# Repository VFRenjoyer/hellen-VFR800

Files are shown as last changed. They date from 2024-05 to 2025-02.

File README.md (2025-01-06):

This repo contains files to build a standalone plug and play RusEFI Hellen based ECU for a 99 Honda VFR800. The prototype is unfinished and currently none of these files can be used to make a functioning ECU

This hardware may be compatible with the CBR600F4i, CBR929RR, and 01-03 CBR1100xx  if the ECU connectors were repinned.

In addition to the above it may be able to replace the ignition module/ECU of a 98-08 VT1100C, 01-07 VT750DC, 02-04 VTX1800, RC51, and 2003-09 VTX1300 with some harness repinning

Features in progress as of v0.05A:

Drop in ECU replacement for 99-01 VFR800 with addition of 2 wideband oxygen sensors

4x sequential ignition/injection

CANBUS

2x Wideband oxygen sensor channels

3x lowside driver output on rear connector

Inputs for analog sensor on rear connector

USB support

Bluetooth connectivity

MicroSD card for logging

VSS input to ECU for eventual implementation of traction control

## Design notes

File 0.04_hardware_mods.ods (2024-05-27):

Modification | Reason
470k resistor between 12V and Tach pin | Tach needs >10v pulses to work
Remove both 22uf capacitors from next to SD card slot | 3.3v current limiting on startup, mentioned on uaEFI github
Replace SMD pull up resistors on MCU analog pins with correct values from uaEFI rev A BOM | Almost all of these are wrong, refer to BOM
Add voltage divider to CRANK/CAM- pin to create +500mV offset | VR Discrete Cam signal drops out at higher frequencies when there’s a signal on the Crank input unless there’s an offset on Cam/Crank negative pin

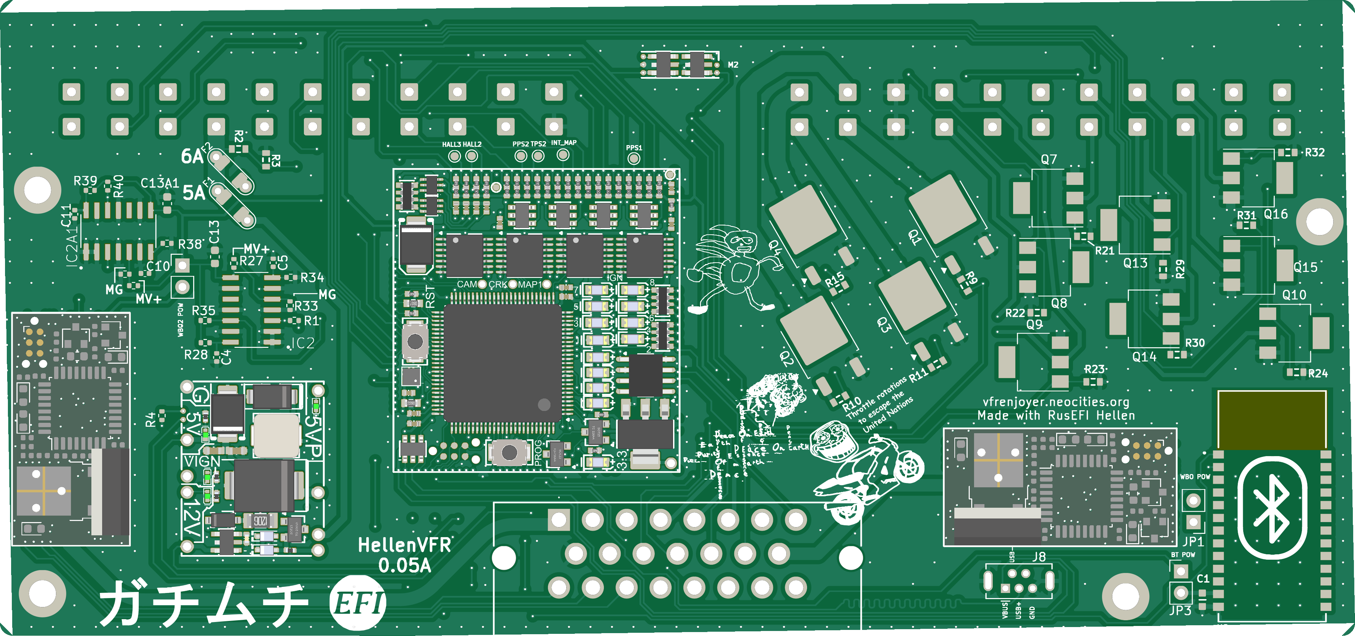
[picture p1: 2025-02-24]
boards/VFRECU-VR-0.05/board/VFRECU-VR-0.05.png

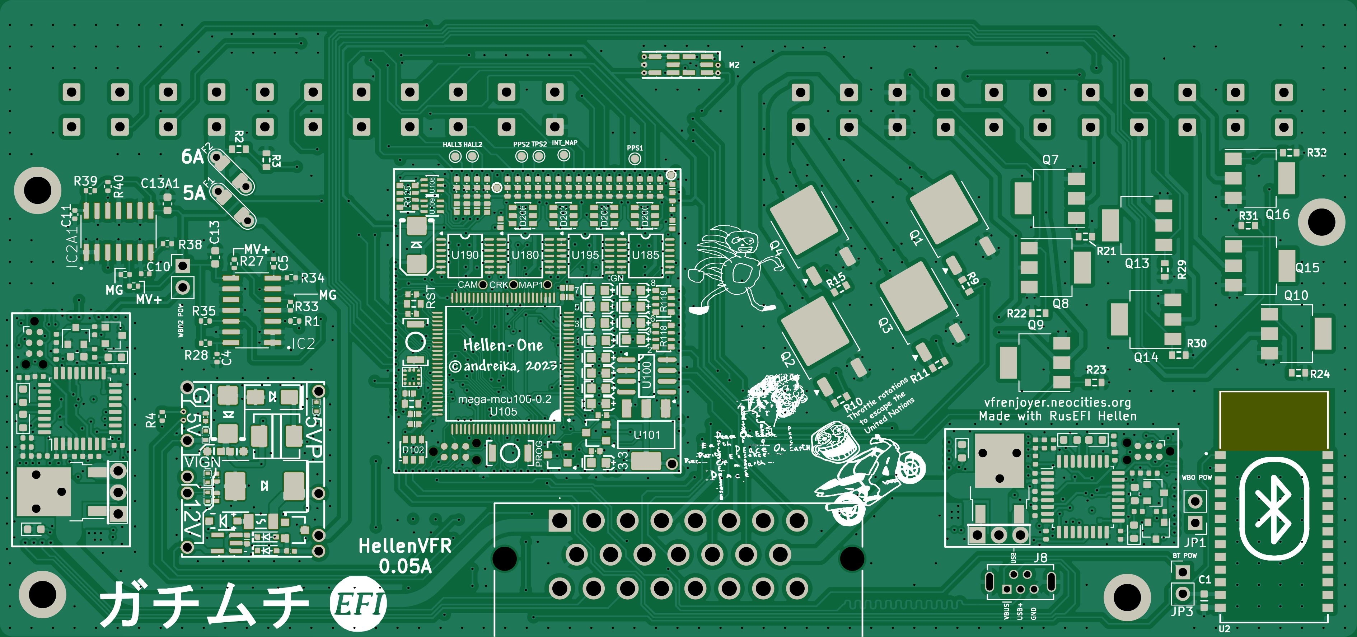
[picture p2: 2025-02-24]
boards/VFRECU-VR-0.05/board/misc/VFRECU-VR-0.05-top.png

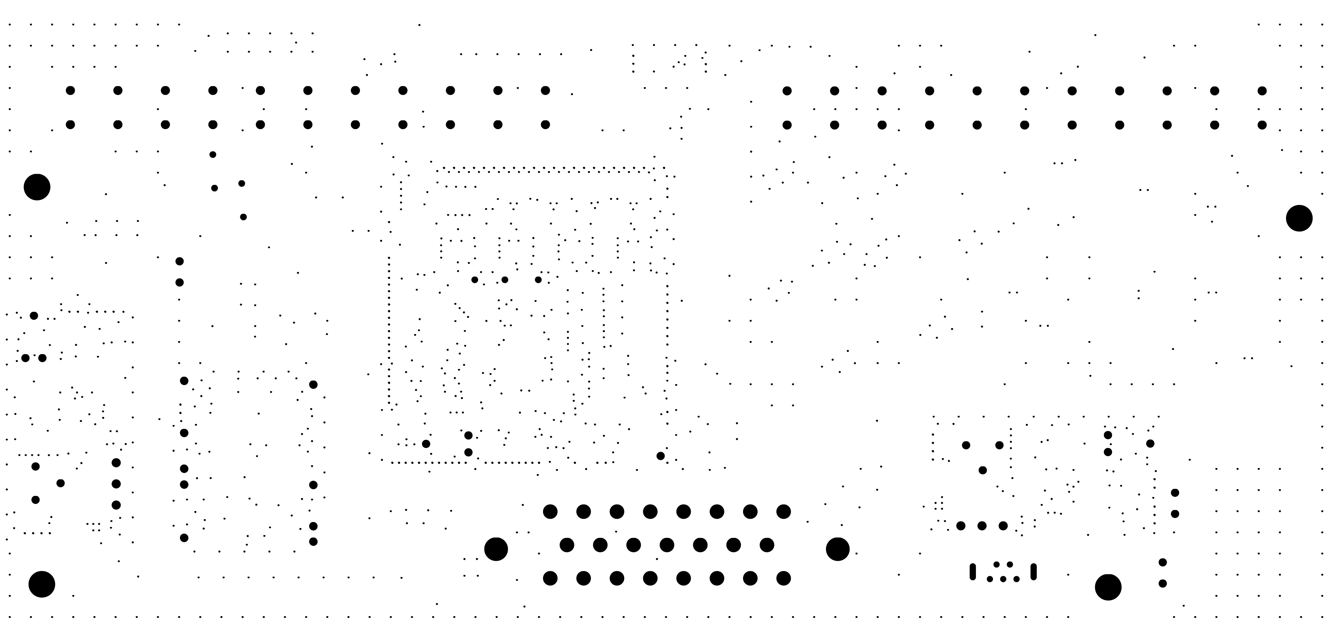
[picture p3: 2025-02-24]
boards/VFRECU-VR-0.05/board/misc/VFRECU-VR-0.05-outline.png

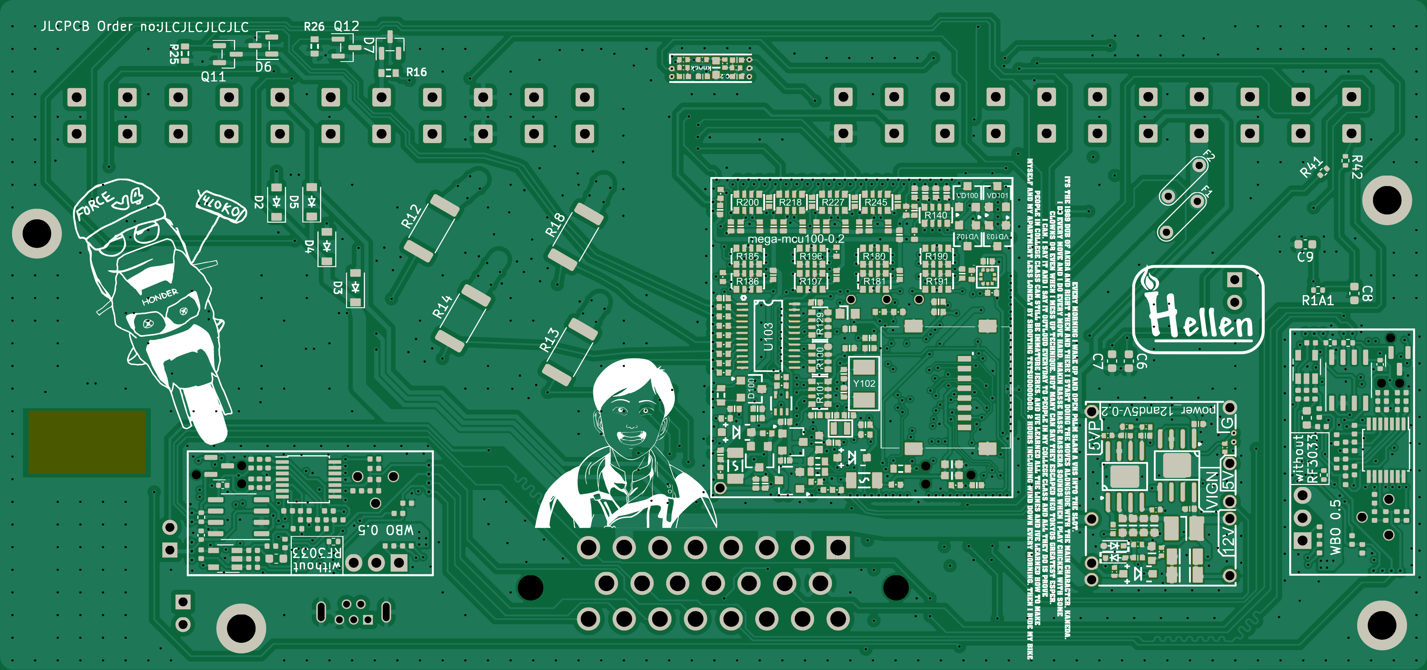
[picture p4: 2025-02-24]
boards/VFRECU-VR-0.05/board/misc/VFRECU-VR-0.05-bottom.png

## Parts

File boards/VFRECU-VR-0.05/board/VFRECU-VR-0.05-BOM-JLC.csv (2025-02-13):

Comment | Designator | Footprint | LCSC Part #
100n | C1 | C0603 | C14663
10u | C13, C13A1, C421, C422, C423, C424, C425, C426 | C0603 | C96446
B5819W | D2, D3, D4, D5, D416, D417, D101, D107 | SOD-123 | C8598
PSM712-LF | D6, D7, D411 | SOT-23 | C32677
12H1500D | F1, F2 | PAD-1206-PAD | C182446
ZXMS6005SGTA | Q7, Q8, Q9, Q10, Q13, Q14, Q15, Q16 | SOT-223 | C174042
AO3400A | Q11, Q12, Q101, Q103 | SOT-23 | C20917
33k | R2, R120 | R0603 | C4216
6.8k | R3 | R0603 | C23212
22 | R9, R10, R11, R15 | R0603 | C23345
0 | R12, R13, R14, R18 | R2512 | C25469
4.7k | R21, R22, R23, R24, R25, R26, R29, R30, R31, R32 | R0603 | C23162
47u | C410, C412 | C1206 | C96123
100n | C411, C413, C420, C470 | C0402 | C307331
1u | C414, C415, C600, C607, C609, C610, C611, C600_2, C607_2, C609_2, C610_2, C611_2 | C0402 | C52923
4.7u | C427, C616, C616_2 | C0603 | C19666
10n | C428, C202, C208, C209, C210, C211, C212, C213, C214, C215 | C0402 | C15195
220p | C429 | C0402 | C1530
1N4148WS | D410, D412, D413, D414 | SOD-323 | C2128
SMCJ30A | D418 | SMC | C310046
SS34 | D420 | SMA | C8678
P6SMB6.8CA | D421, D205 | SMB | C78395
SMD1206P050TF/24 | F410 | SMD1206 | C209741
2.2uH | L420 | L1210 | C36828
MWSA0503-10uH | L421 | MWSA0503 | C139506
MHT136UGCT | LED1, LED2, LED3, LED4 | LED0402 | C434447
6.8k | R410, R413 | R0402 | C25917
33k | R411, R424, R425, R474 | R0402 | C25779
1 | R420 | R0402 | C25086
10k | R421, R426, R427, R604, R605, R613, R614, R618, R619, R625, R102, R103, R105, R107, R108, R109, R121, R124, R126, R127, R128, R132, R135, R136, R137, R138, R139, R141, R142, R228, R229, R230, R231, R232, R233, R234, R235, R246, R247, R248, R249, R250, R251, R252, R253, R604_2, R605_2, R613_2, R614_2, R618_2, R619_2, R625_2 | R0402 | C25744
68k | R422, R602, R603, R602_2, R603_2 | R0402 | C36871
12k | R423, R472 | R0402 | C25752
4.7k | R428, R144, R203, R204, R207, R208, R219, R220, R223, R224 | R0402 | C25900
MIC5205-3.3YM5 | U410 | SOT23-5 | C37970
TLS115 | U411 | PG-DSO-8 EP | C540242
LMR14020 | U420 | SOP8 | C187824
3.3n | C471 | C0402 | C26404
330p | C472 | C0402 | C13533
47p | C473 | C0402 | C1567
680p | C474 | C0603 | C1630
470k | R470 | R0402 | C25790
100k | R471, R473, R615, R621, R615_2, R621_2 | R0402 | C25741
LMV321IDBVR | U470, U471 | SOT23-5 | C7972
100n | C601, C602, C605, C608, C612, C613, C614, C615, C617, C618, C100, C101, C105, C108, C111, C112, C113, C119, C120, C122, C124, C126, C127, C130, C134, C147, C180, C185, C190, C195, C220, C221, C222, C601_2, C602_2, C605_2, C608_2, C612_2, C613_2, C614_2, C615_2, C617_2, C618_2 | C0402 | C1525
33n | C603, C603_2 | C0402 | C1585
LED-RED-0603 | D600, D603, D103, D600_2, D603_2 | LED-0603 | C2286
LED-GREEN-0603 | D601, D104, D108, D601_2 | LED-0603 | C72043
LED-BLUE-0603 | D602, D105, D109, D110, D111, D112, D113, D114, D115, D116, D602_2 | LED-0603 | C72041
PESD1CAN | D604, D100, D604_2 | SOT-23 | C343993
VND7NV04TR-E | Q600, Q600_2 | DPAK | C155605
1k | R600, R601, R616, R617, R622, R626, R627, R628, R600_2, R601_2, R616_2, R617_2, R622_2, R626_2, R627_2, R628_2 | R0402 | C11702
10 | R606, R110, R111, R112, R113, R114, R115, R116, R117, R606_2 | R0402 | C25077
22k | R607, R607_2 | R0402 | C25768
47 | R608, R608_2 | R0402 | C25118
61.9 | R609, R609_2 | R0603 | C23092
20k | R610, R611, R612, R610_2, R611_2, R612_2 | R0402 | C25765
27k | R620, R623, R620_2, R623_2 | R0402 | C25771
3.3k | R624, R624_2 | R0402 | C25890
MCP6004 | U600, U180, U185, U190, U195, U600_2 | TSSOP14 | C50282
AD8628 | U601, U601_2 | TSOT23-5 | C29309
STM32F042K6Tx | U602, U602_2 | LQFP32 | C69216
REF3033 | U603, U102, U603_2 | SOT-23 | C36658
XC6206P332MR | U604, U604_2 | SOT-23 | C5446
TJA1051T/3/1J | U605, U100, U605_2 | SO-8_3.9x4.9mm_P1.27mm | C38695
STM32F429VGT6 | U105 | LQFP100 | C95448
SRV05-4-P-T7 | D102, D200, D202, D203, D206 | SOT23-6 | C85364
SN74LVC4245APWR | U103 | TSSOP24 | C7859
SN74LVC1G06DCKR | U110 | SOT-353 | C7828
SMD1206B035TF/16 | F100, F101 | R1206 | C269114
Molex MicroSD 47219-2001 | J100 | SDAMB-012 | C164170
LPS22HBTR | U107 | HLGA-10L | C94049
LIS2DH12TR | U106 | LGA12 | C110926
LED-YELLOW-0603 | D106 | LED-0603 | C72038
LDL1117S33R | U101 | SOT-223 | C435835
BTN | S100, S101 | SMD-2_2.9x3.9x1.7 | C115357
BLM18AG601SN1D | L100 | L0603 | C19330
BAT54S | VD100, VD101, VD102, VD103 | SOT-23 | C47546
AO3401A | Q100, Q102 | SOT-23 | C15127
680k | R201, R202, R205, R206, R221, R222, R225, R226 | R0402 | C163456
510 | R133, R134 | R0603 | C23193
510 | R254, R255, R256, R258 | R0402 | C25123
470 | R101, R118, R119 | R0603-4 | C25510
120 | R100 | R0603 | C22787
100 | R104, R106 | R0603 | C22775
74LVC2G17GW,125 | U108, U109 | SOT-363 | C80500
32.768 kHz | Y101 | SMD2012 | C99009
22u | C117, C123 | C0603 | C59461
20 MHz | Y102 | SMD5032 | C112566
18p | C132, C136 | C0402 | C1549
12p | C115, C116 | C0402 | C1547
10k | R129, R130, R140 | R0603-4 | C29718
5.1k | R195 | R0402 | C25905
4.7u | C102, C103, C104, C106, C107, C137, C138, C140 | C0402 | C23733
4.7k | R125, R180, R181, R185, R186, R190, R191, R196, R197, R200, R218, R227, R245 | R0603-4 | C66697
2.2u | C114, C131, C223, C224, C229 | C0402 | C12530
2.2k | R122, R123, R146, R147 | R0402 | C25879
1u | C133 | C0603 | C519560
1n | C135, C139, C141, C142, C143, C144, C145, C146, C200, C201, C203, C225, C226, C227, C228 | C0402 | C1523
0 | R131, R143, R145, R148 | R0402 | C17168

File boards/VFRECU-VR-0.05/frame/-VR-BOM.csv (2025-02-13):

Comment | Designator | Footprint | LCSC Part #
100n | C1 | C0603 | C14663
1.2n | C4 | C0402
0.33u | C5 | C0402
~ | C6 | C0603
0.33u | C7 | C0603
0.33u | C8 | C0603
~ | C9 | C0603
0.33u | C10 | C0402
1.2n | C11 | C0402
10u | C13 | C0603 | C96446
10u | C13A1 | C0603 | C96446
B5819W | D2 | SOD-123 | C8598
B5819W | D3 | SOD-123 | C8598
B5819W | D4 | SOD-123 | C8598
B5819W | D5 | SOD-123 | C8598
PSM712-LF | D6 | SOT-23 | C32677
PSM712-LF | D7 | SOT-23 | C32677
12H1500D | F1 | PAD-1206-PAD | C182446
12H1500D | F2 | PAD-1206-PAD | C182446
RUSEFI_LOGO | G3 | rusefi_logo
LOGO | G4 | LOGO
MountingHole_Pad | H1 | MountingHole_3.2mm_M3_DIN965_Pad
MountingHole_Pad | H2 | MountingHole_3.2mm_M3_DIN965_Pad
MountingHole_Pad | H3 | MountingHole_3.2mm_M3_DIN965_Pad
MountingHole_Pad | H4 | MountingHole_3.2mm_M3_DIN965_Pad
LM1815MX_NOPB | IC2 | SOIC127P600X175-14N
LM1815MX_NOPB | IC2A1 | SOIC127P600X175-14N
1-776087-1 | J4 | 17760871
USB_B_Mini | J8 | USB-MINI-B-VERTICAL
Jumper_2_Bridged | JP1 | PinHeader_1x02_P2.54mm_Vertical
Jumper_2_Bridged | JP2 | PinHeader_1x02_P2.54mm_Vertical
Jumper_2_Bridged | JP3 | PinHeader_1x02_P2.54mm_Vertical
Module:power_12and5V/0.2 | M1 | power_12and5V
Module:knock/0.2 | M2 | knock
Module:wbo/0.5 | M5 | wbo
Module:mega-mcu100/0.2 | M6 | mega-mcu100
Module:wbo/0.5 | M7 | wbo
ISL9V3040D3S | Q1 | DPAK
ISL9V3040D3S | Q2 | DPAK
ISL9V3040D3S | Q3 | DPAK
ISL9V3040D3S | Q4 | DPAK
ZXMS6005SGTA | Q7 | SOT-223 | C174042
ZXMS6005SGTA | Q8 | SOT-223 | C174042
ZXMS6005SGTA | Q9 | SOT-223 | C174042
ZXMS6005SGTA | Q10 | SOT-223 | C174042
AO3400A | Q11 | SOT-23 | C20917
AO3400A | Q12 | SOT-23 | C20917
ZXMS6005SGTA | Q13 | SOT-223 | C174042
ZXMS6005SGTA | Q14 | SOT-223 | C174042
ZXMS6005SGTA | Q15 | SOT-223 | C174042
ZXMS6005SGTA | Q16 | SOT-223 | C174042
4.7k | R1 | R0402
4.7k | R1A1 | R0402
33k | R2 | R0603 | C4216
6.8k | R3 | R0603 | C23212
0 | R4 | R0402
22 | R9 | R0603 | C23345
22 | R10 | R0603 | C23345
22 | R11 | R0603 | C23345
0 | R12 | R2512 | C25469
0 | R13 | R2512 | C25469
0 | R14 | R2512 | C25469
22 | R15 | R0603 | C23345
470k | R16 | R0603
0 | R18 | R2512 | C25469
4.7k | R21 | R0603 | C23162
4.7k | R22 | R0603 | C23162
4.7k | R23 | R0603 | C23162
4.7k | R24 | R0603 | C23162
4.7k | R25 | R0603 | C23162
4.7k | R26 | R0603 | C23162
0 | R27 | R0402
100k | R28 | R0402
4.7k | R29 | R0603 | C23162
4.7k | R30 | R0603 | C23162
4.7k | R31 | R0603 | C23162
4.7k | R32 | R0603 | C23162
0 | R33 | R0402
1.6M | R34 | R0402
5.6k | R35 | R0402
0 | R36 | R0402
0 | R37 | R0402
1.6M | R38 | R0402
100k | R39 | R0402
5.6k | R40 | R0402
0 | R41 | R0402
0 | R42 | R0402
~ | text1 | trollfaceVFR
~ | U1 | VFRboardempty
JDY-33 | U2 | JDY-33

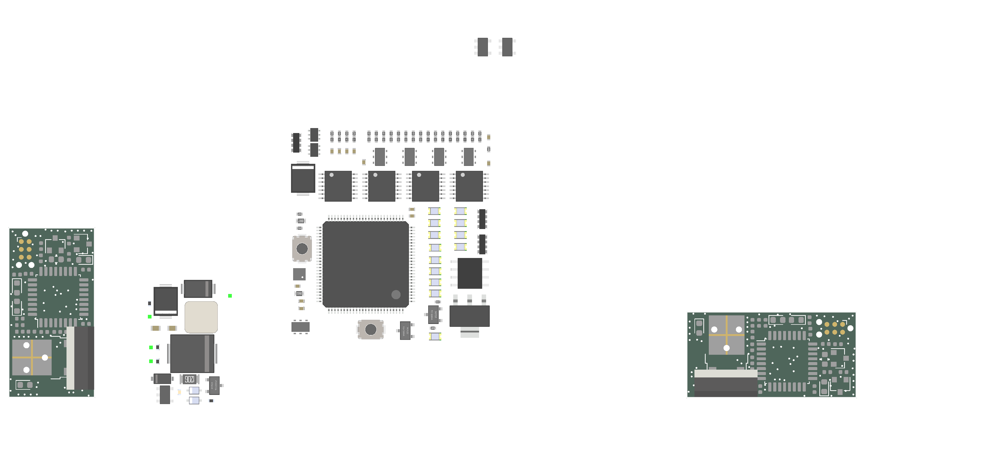
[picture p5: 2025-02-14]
boards/VFRECU-VR-0.05/board/misc/VFRECU-VR-0.05-components.png

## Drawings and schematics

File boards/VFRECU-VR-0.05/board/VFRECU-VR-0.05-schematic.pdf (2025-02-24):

# IN3 Ignition GND

# +5V ¹ ²

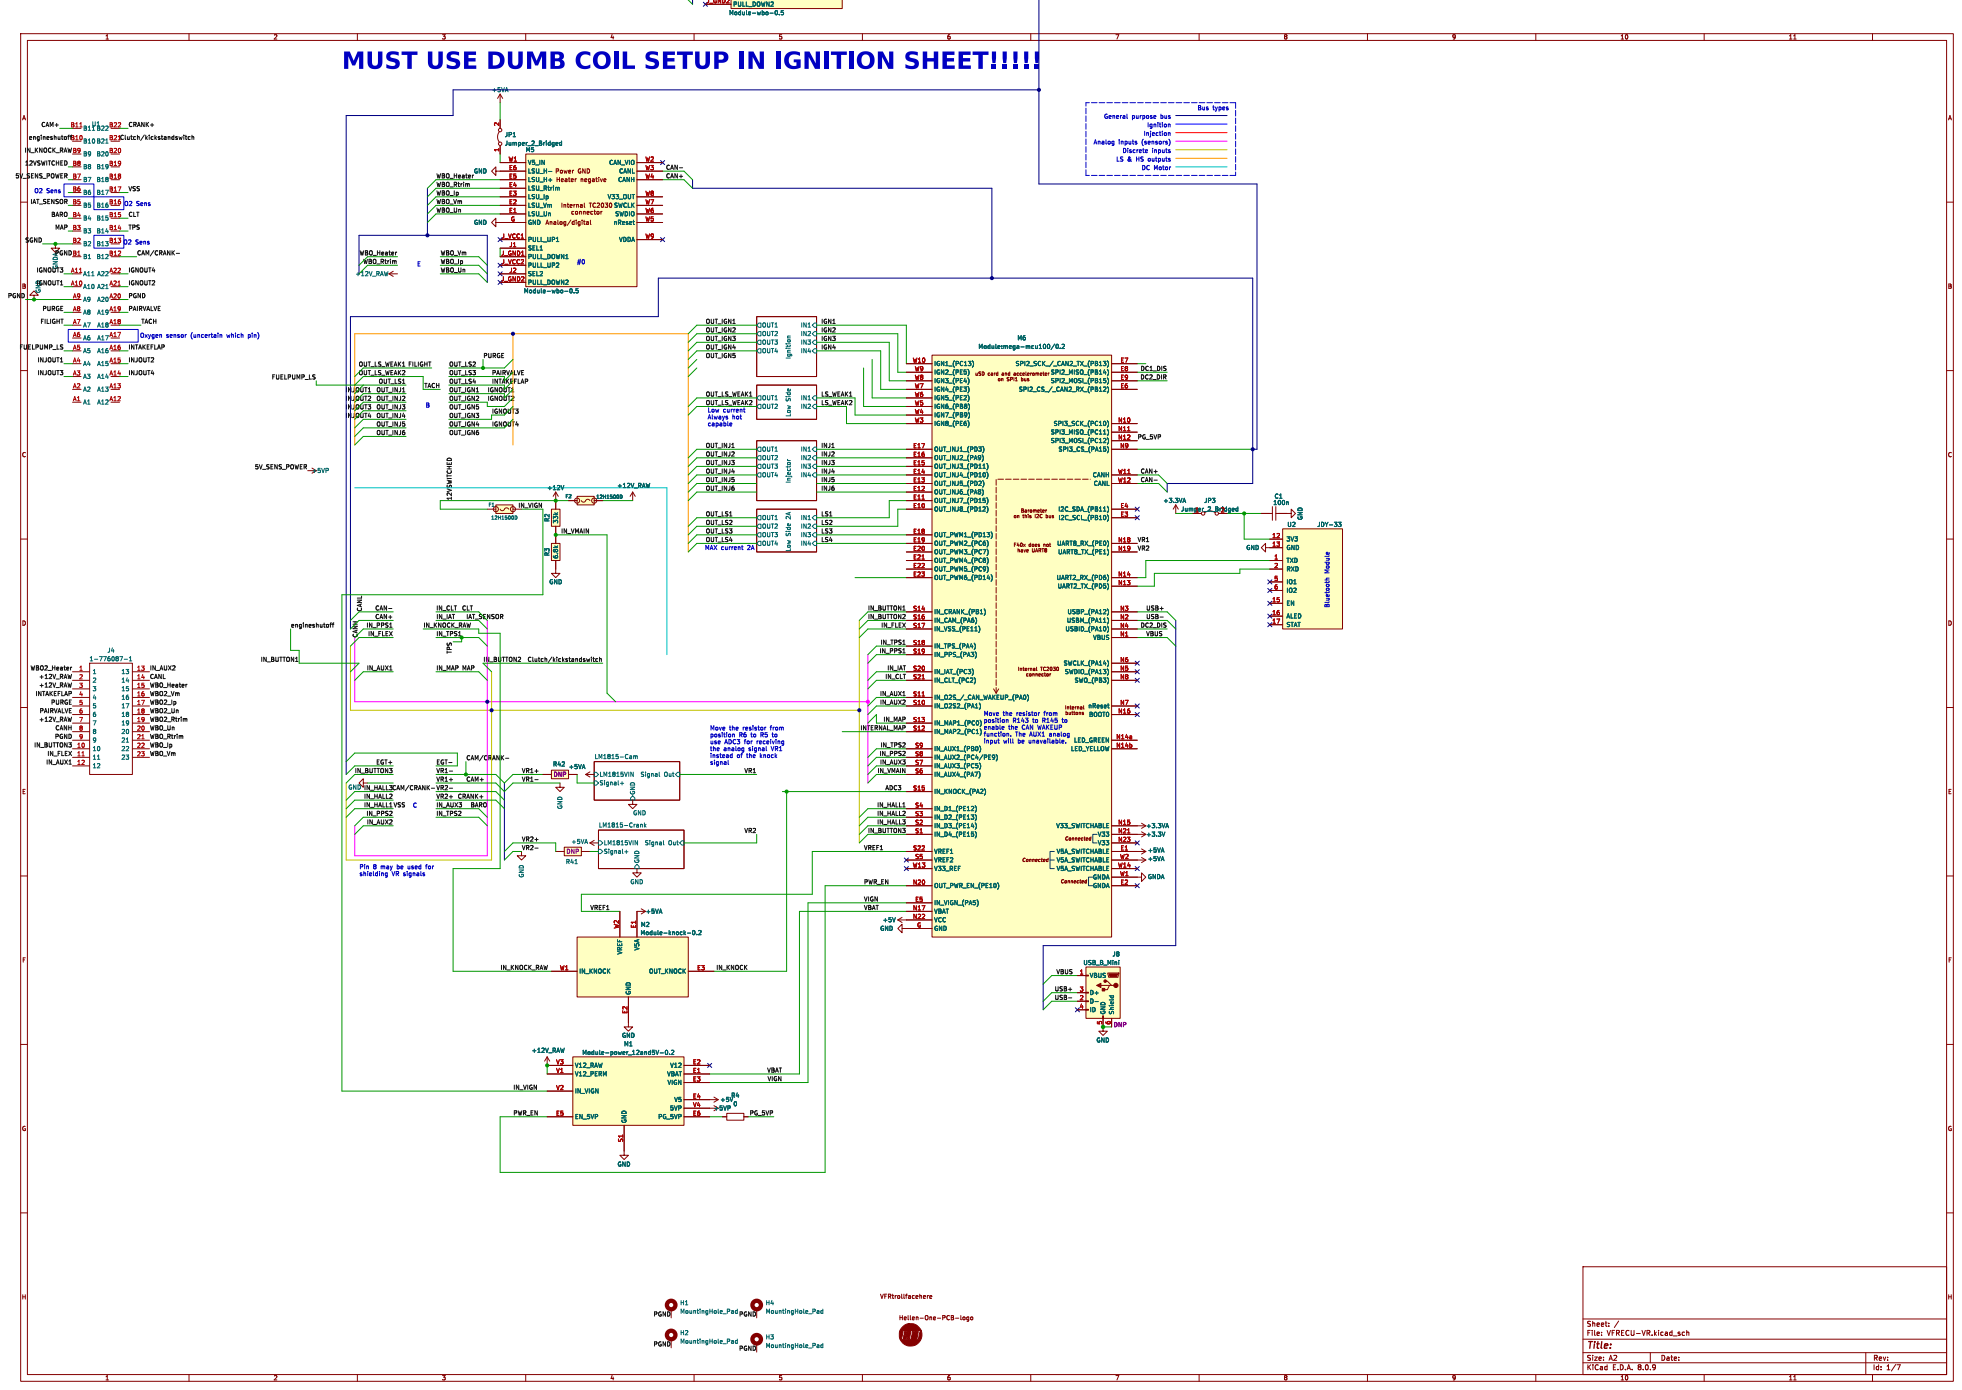
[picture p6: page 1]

Analog/digital Heater negative Power GND

Low current Always hot capable

enable the CAN WAKEUP
input will be unavailable.

use ADC3 for receiving
the analog signal VR1
instead of the knock
signal

Hellen-One-PCB-logo H4 MountingHole_Pad GND

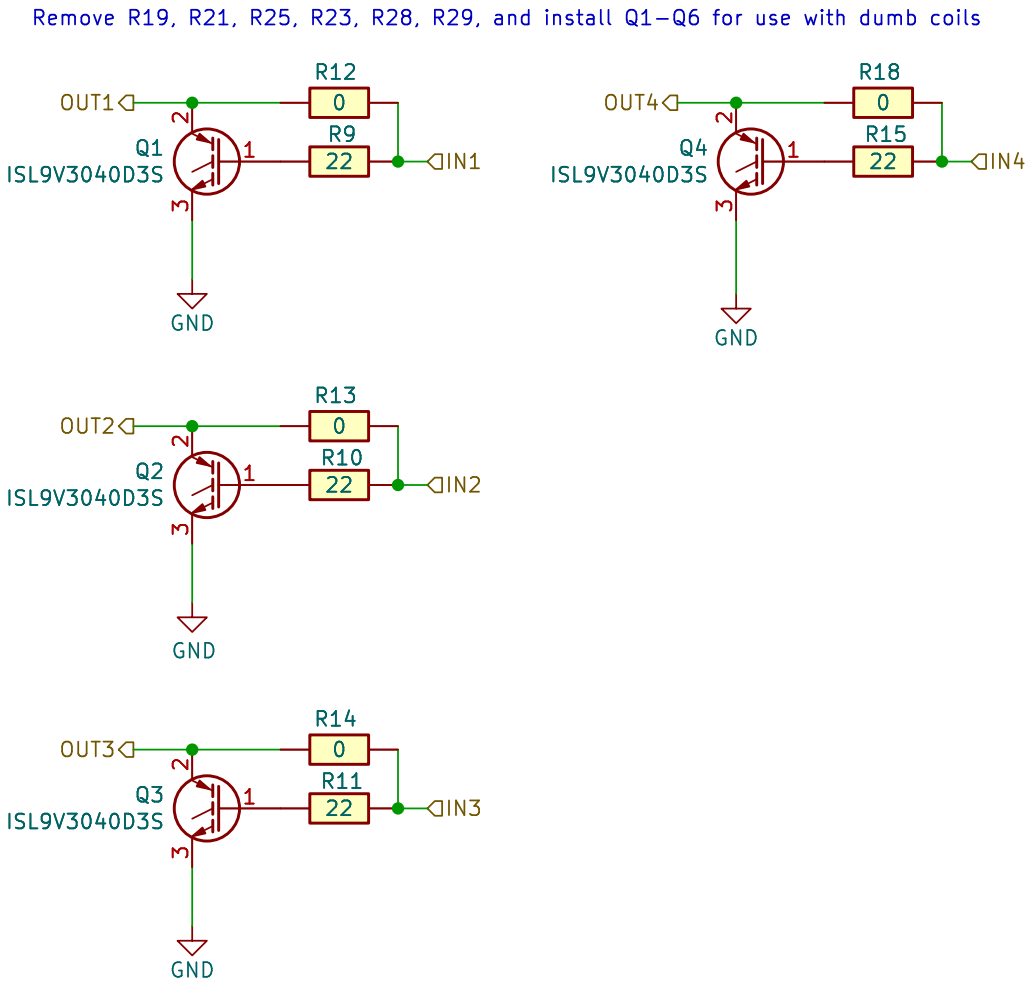
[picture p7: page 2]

File: IGN6.kicad_sch Sheet: /Ignition/ rusefi.com

Id: 2/7 Title: UAEFI Ignition

# 10u GND

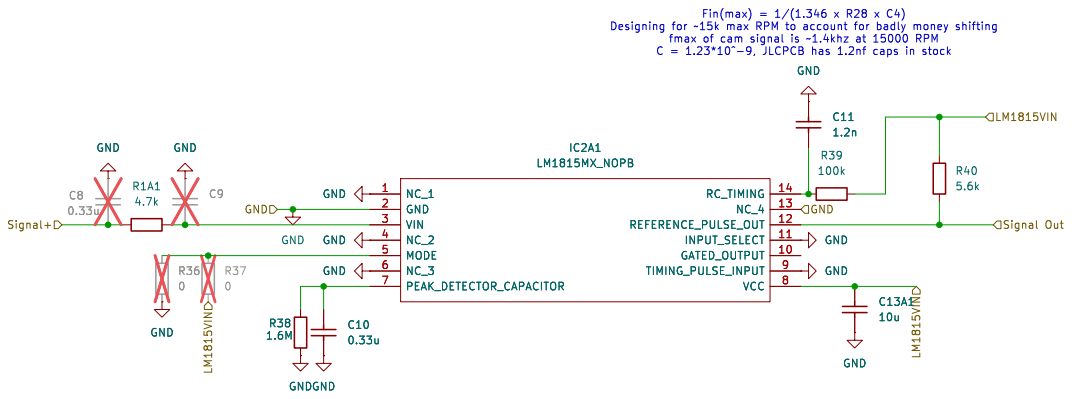
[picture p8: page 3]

fmax of cam signal is ~1.4khz at 15000 RPM

Id: 3/7 Title: File: LM1815-Cam.kicad_sch Sheet: /LM1815-Cam/

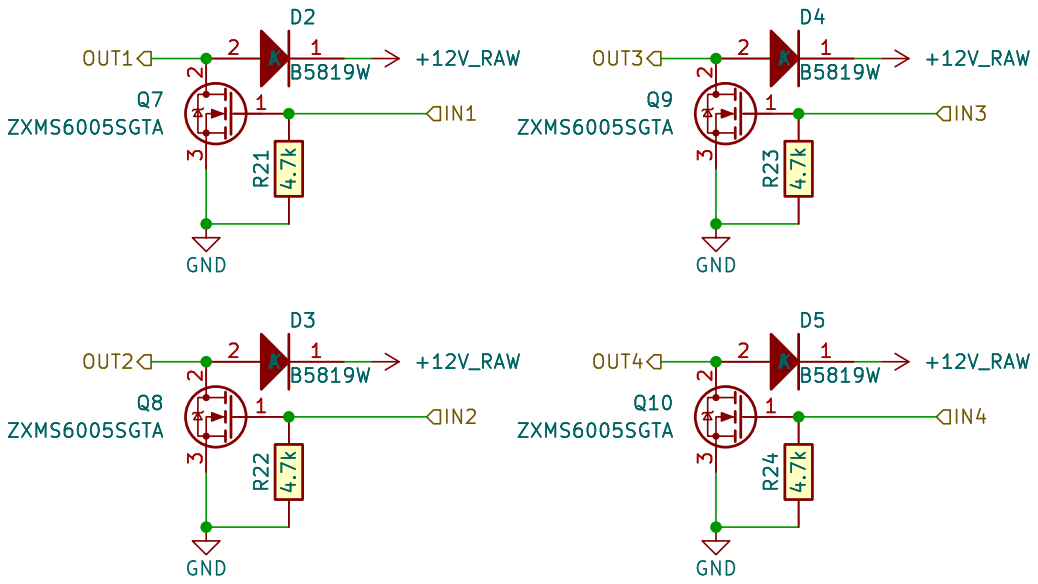
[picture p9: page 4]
D Date: 2023-11-01 KiCad; E.D.A. 8.0.9 Size: A4; Rev:; 2 3 Q10 ZXMS6005SGTA R21 4.7k 1; 2 3 Q7 ZXMS6005SGTA R22 4.7k K; +12V_RAW; GND; 2 3 Q9 ZXMS6005SGTA GND; +12V_RAW 1 A; D4B5819W R²³ 4.7k 1; 2 3 Q8 ZXMS6005SGTA GND; D5B5819W R²⁴ 4.7k; OUT3 OUT2 OUT1; OUT4; IN3 +12V_RAW; 2 R²⁴ 4.7k R²³ 4.7k; 2 Q10 ZXMS6005SGTA; 2 3 Q9 ZXMS6005SGTA; 2 3 +12V_RAW; 2 R²² 4.7k R²¹ 4.7k Q7 ZXMS6005SGTA 1; 2 Q8 ZXMS6005SGTA

File: LS4.kicad_sch Sheet: /Low Side 2A/ rusefi.com

Id: 4/7 Title: UAEFI Low Side

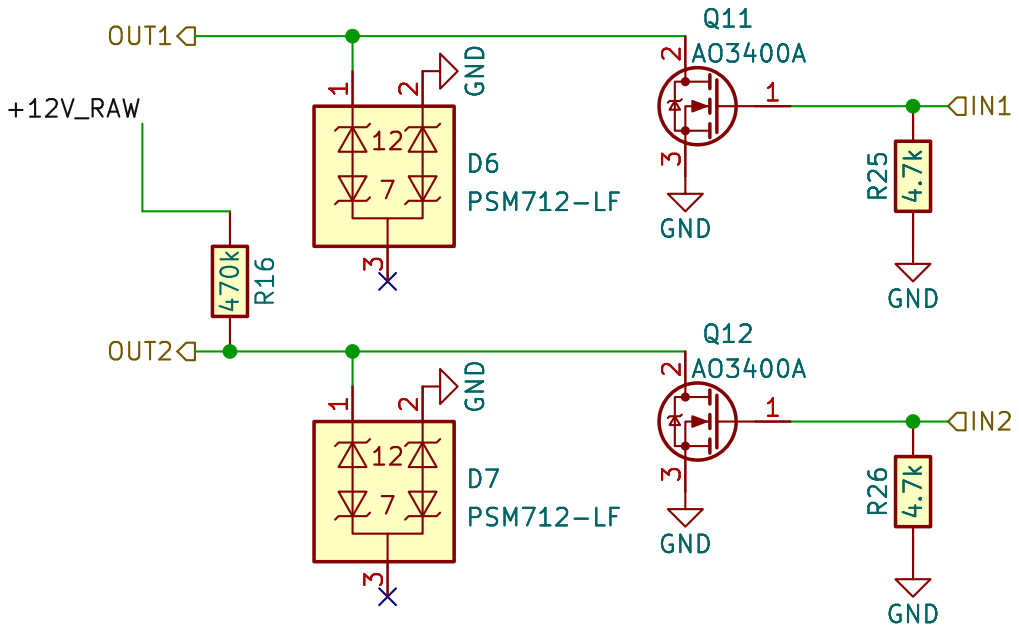
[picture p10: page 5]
D Date: 2023-11-01 KiCad; E.D.A. 8.0.9 Size: A4; Rev:; GND; 2 3 Q11 AO3400A GND GND; 3 D7PSM712-LF R25 4.7k OUT1; IN1 IN2 OUT2 +12V_RAW; 2 3 GND GND; D6PSM712-LF; 3 GND R25 4.7k D7PSM712-LF; 3 GND R26 4.7k GND Q12 AO3400A; 2 3 GND

3 D6PSM712-LF GND R26 4.7k 470k R16 GND GND

Id: 5/7 Title: UAEF Low Side low current File: LS_weak.kicad_sch Sheet: /Low Side/ rusefi.com

0 | C6 GND
1.2n GND | GND GND

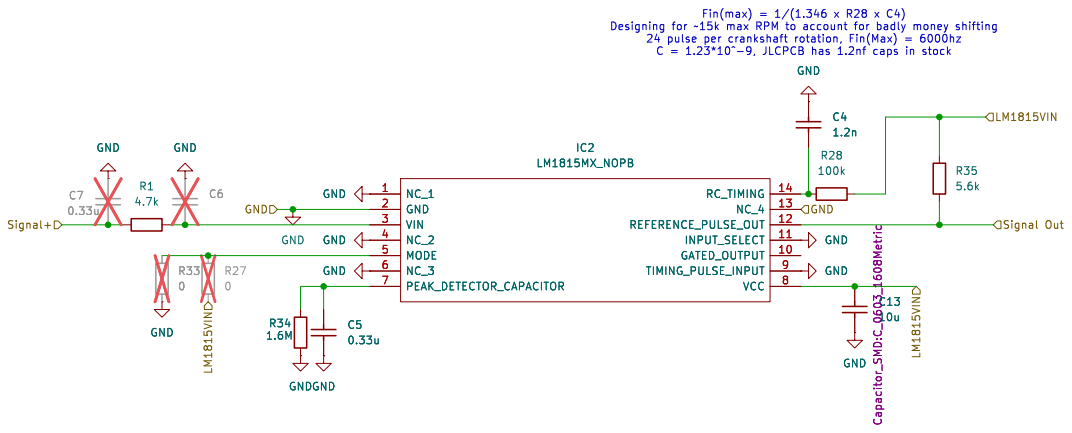
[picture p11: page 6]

Id: 6/7 Title: File: LM1815.kicad_sch Sheet: /LM1815-Crank/

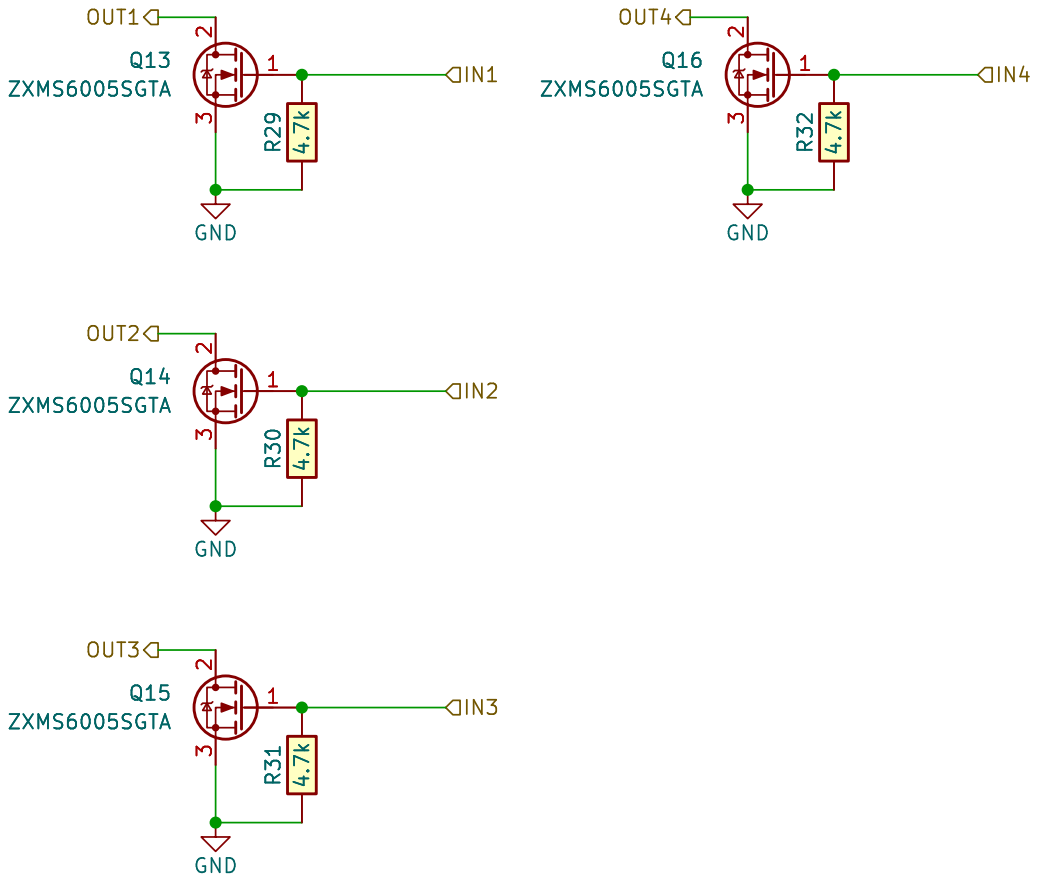
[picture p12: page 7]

Id: 9/7 Title: UAEFI Injector File: INJ6.kicad_sch Sheet: /Injector/ rusefi.com

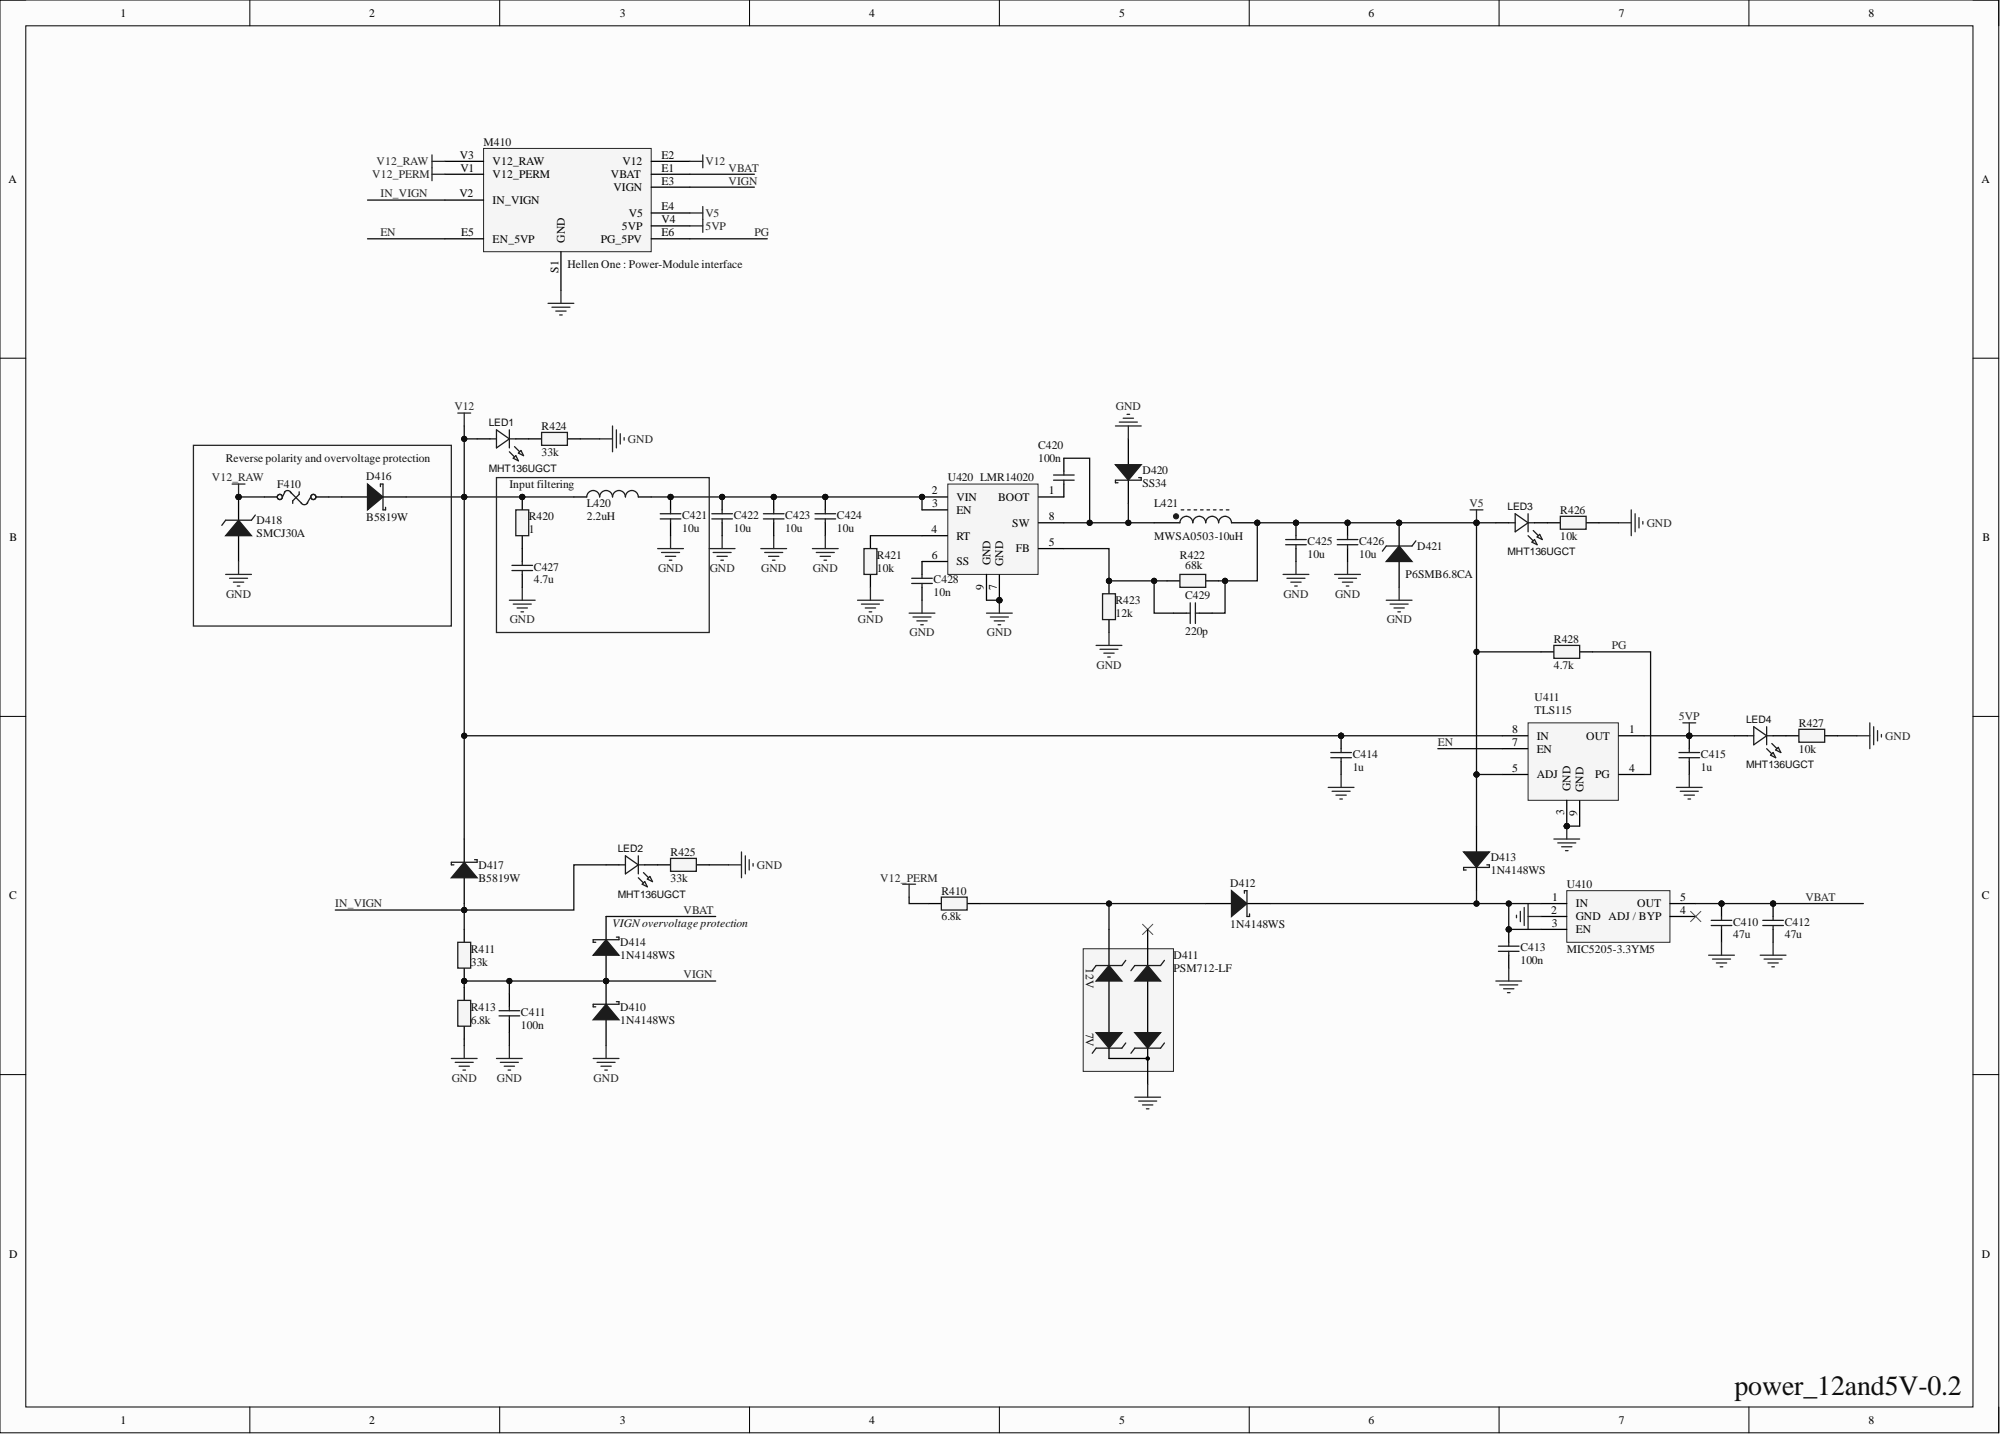
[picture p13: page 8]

Hellen One : Power-Module interface

Reverse polarity and overvoltage protection
F410 V12_RAW

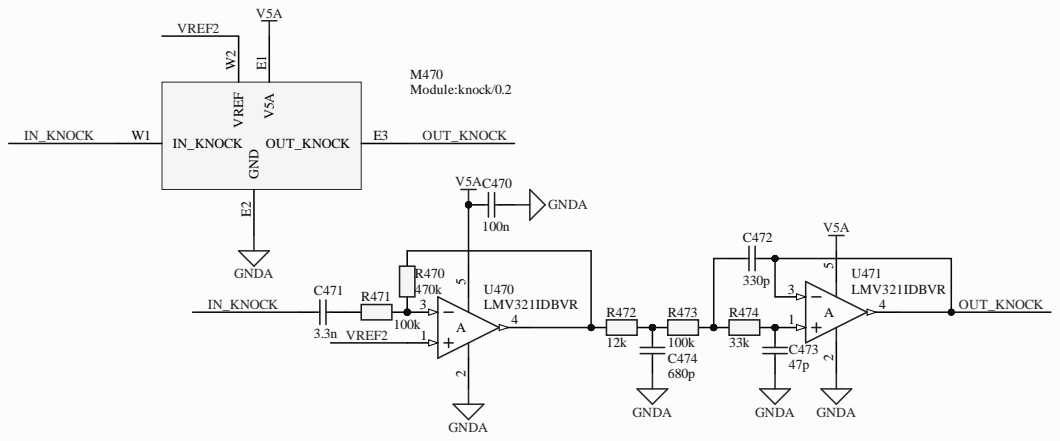
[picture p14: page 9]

+3.3V C616

27k +

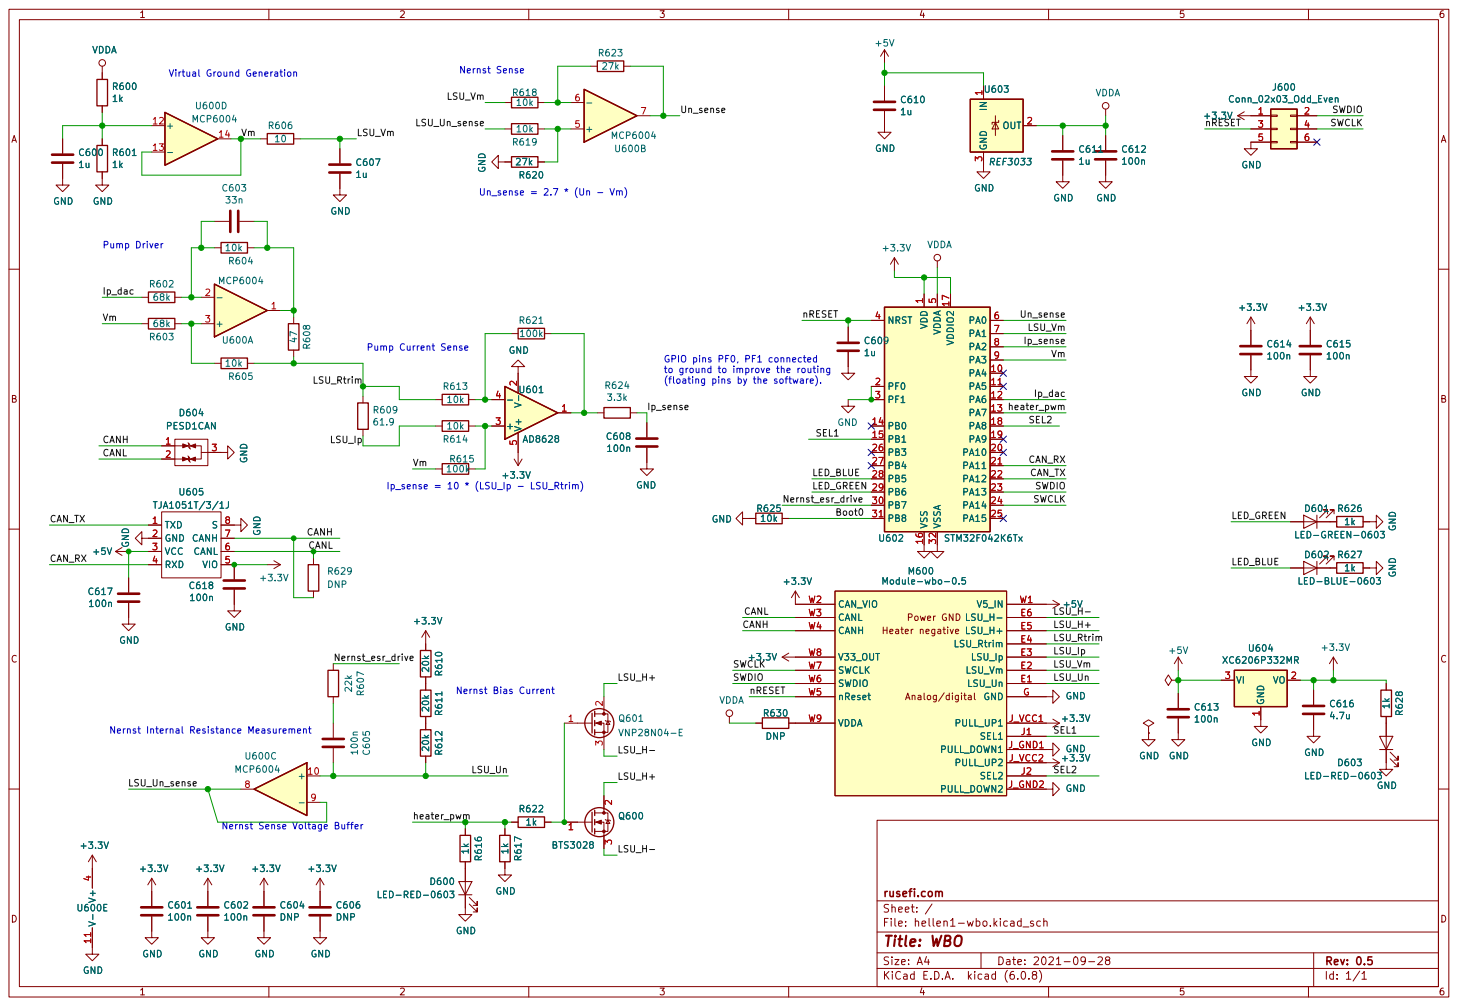
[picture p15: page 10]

100n GND GND R⁶⁰⁸ ⁴⁷

1 PA4 10 PA5 11 PA6 12 PA7 13 PB0 14 PB1 15 VSS 16 VDDIO2 17 PA8 18 PA9 19 PF0 2 PA10 20 PA11 21 PA12 22 PA13 23 PA14 24 PA15 25 PB3 26 PB4 27 PB5 28 PB6 29 PF1 3 PB7 30 PB8 31 VSSA 32 NRST 4 VDDA

1u GND GND GND
+3.3V R⁶¹¹ ²⁰k R⁶¹⁰ ²⁰k GND

to ground to improve the routing
(floating pins by the software).

Heater negative Power GND

VDDA GND
Nernst Sense Voltage Buffer Nernst Internal Resistance Measurement

+3.3V C606 DNP GND
File: hellen1-wbo.kicad_sch Sheet: / rusefi.com V⁻ 11 V⁺

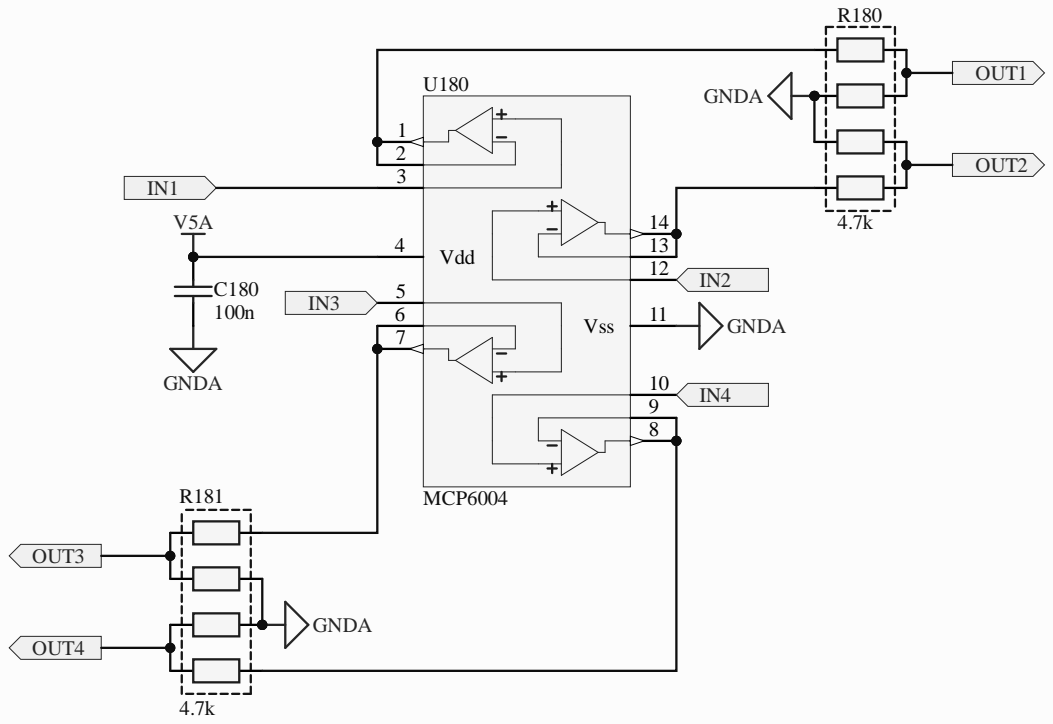
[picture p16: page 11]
Vdd 4; Vss 6; MCP6004; GNDA; OUT1; OUT2; OUT3; OUT4; C180 PIC18001 100n; PIC18002 COC3; PIR18001; PIR18002; PIR18003; PIR18004; PIR18005; PIR18006; PIR18007; PIR18008; COR5; PIR18101; PIR18102; PIR18103; PIR18105; PIR18104; PIR18106; PIR18107; PIR18108; COR6; PIU18001; PIU18002; PIU18003; PIU18004; PIU18005; PIU18006; PIU18007; PIU18008; PIU18009; PIU180010; PIU180011; PIU180012; PIU180013; PIU180014; COU2; PIC18001; POOUT2; POOUT1; POOUT3; POOUT4; POIN1; POIN3 PIU18005; PIU180010 POIN4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

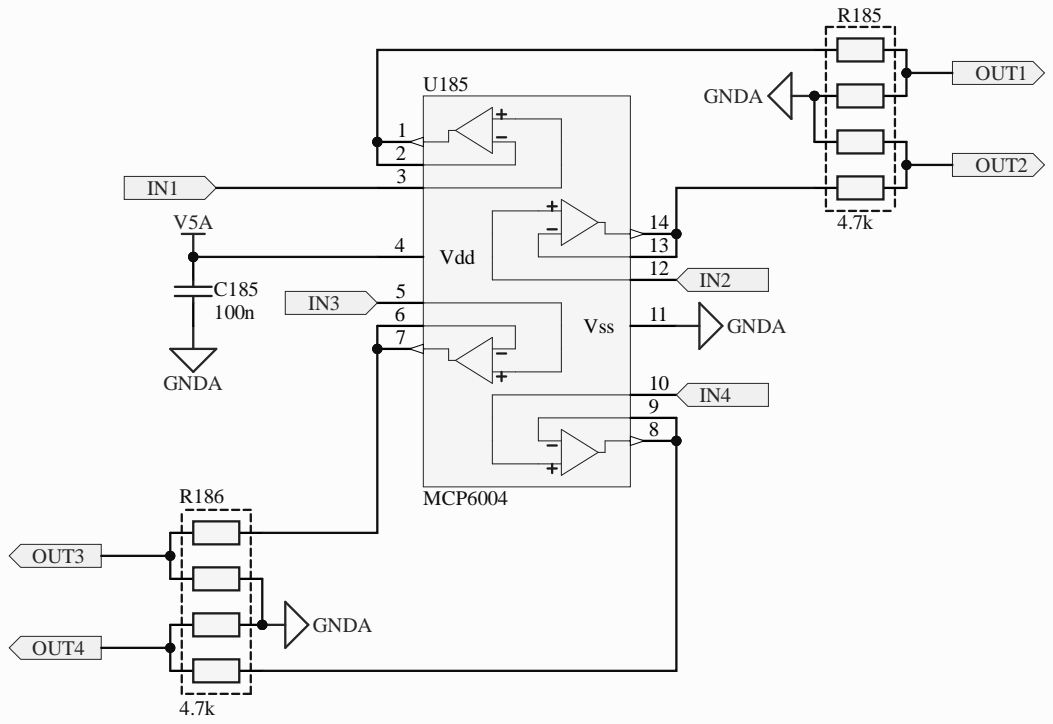
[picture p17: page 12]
Vdd 4; Vss 6; MCP6004; GNDA; OUT1; OUT2; OUT3; OUT4; C185 PIC18501 100n; PIC18502 COC3; PIR18501; PIR18502; PIR18503; PIR18504; PIR18505; PIR18506; PIR18507; PIR18508; COR5; PIR18601; PIR18602; PIR18603; PIR18605; PIR18604; PIR18606; PIR18607; PIR18608; COR6; PIU18501; PIU18502; PIU18503; PIU18504; PIU18505; PIU18506; PIU18507; PIU18508; PIU18509; PIU185010; PIU185011; PIU185012; PIU185013; PIU185014; COU2; PIC18501; POOUT2; POOUT1; POOUT3; POOUT4; POIN1; POIN3 PIU18505; PIU185010 POIN4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

Vdd 4; Vss 6; MCP6004; GNDA; OUT1; OUT2; OUT3; OUT4; C190 PIC19001 100n; PIC19002 COC3; PIR19001; PIR19002; PIR19003; PIR19004; PIR19005; PIR19006; PIR19007; PIR19008; COR5; PIR19101; PIR19102; PIR19103; PIR19105; PIR19104; PIR19106; PIR19107; PIR19108; COR6; PIU19001; PIU19002; PIU19003; PIU19004; PIU19005; PIU19006; PIU19007; PIU19008; PIU19009; PIU190010; PIU190011; PIU190012; PIU190013; PIU190014; COU2; PIC19001; POOUT2; POOUT1; POOUT3; POOUT4; POIN1; POIN3 PIU19005; PIU190010 POIN4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

SPI_; VCC; 5 SPI_SCK; 7 SPI_O; lex MicroSD; _MIS


R143 populated: analog input O2S
R145 populated: WAKEUP by CAN

*VIGN input is unprotected!
*A21 is duplicated for ADC and EINT




D100 PESD1CAN; GND; TXD 1 GND 2 VCC 3; Vio; 5 RXD 4; CANL; 6 CANH; TJA1051T/3/1J; CAN_TX; CAN_RX; VCC; CANH; CANL C100 100n
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

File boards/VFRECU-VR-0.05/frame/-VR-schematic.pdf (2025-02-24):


Analog/digital Heater negative Power GND

Low current Always hot capable

enable the CAN WAKEUP
input will be unavailable.

use ADC3 for receiving
the analog signal VR1
instead of the knock
signal

Hellen-One-PCB-logo H4 MountingHole_Pad GND


File: IGN6.kicad_sch Sheet: /Ignition/ rusefi.com

Id: 2/7 Title: UAEFI Ignition


fmax of cam signal is ~1.4khz at 15000 RPM

Id: 3/7 Title: File: LM1815-Cam.kicad_sch Sheet: /LM1815-Cam/


File: LS4.kicad_sch Sheet: /Low Side 2A/ rusefi.com

Id: 4/7 Title: UAEFI Low Side


3 D6PSM712-LF GND R26 4.7k 470k R16 GND GND

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


Id: 6/7 Title: File: LM1815.kicad_sch Sheet: /LM1815-Crank/


Id: 9/7 Title: UAEFI Injector File: INJ6.kicad_sch Sheet: /Injector/ rusefi.com

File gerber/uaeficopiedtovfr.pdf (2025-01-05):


MUST USE DUMB COIL SETUP IN IGNITION SHEET!!!!!

DC Motor LS & HS outputs

Analog/digital Heater negative Power GND

Low current Always hot capable

enable the CAN WAKEUP
input will be unavailable.

use ADC3 for receiving
the analog signal VR1
IN_PPS2 VR1_A
instead of the knock

VBUS USB- VBAT VIGN


File: IGN6.kicad_sch Sheet: /Ignition/ rusefi.com

Id: 2/5 Title: UAEFI Ignition


File: LS4.kicad_sch Sheet: /Low Side 2A/ rusefi.com

Id: 4/5 Title: UAEFI Low Side


3 D6PSM712-LF GND R26 4.7k 470k R16 GND GND

Id: 5/5 Title: UAEF Low Side low current File: LS_weak.kicad_sch Sheet: /Low Side/ rusefi.com


Id: 9/5 Title: UAEFI Injector File: INJ6.kicad_sch Sheet: /Injector/ rusefi.com

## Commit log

2024-04-19 [skip actions] Auto-generated board v2.1
    [uaeficopiedtovfr-B_Cu.gbl, uaeficopiedtovfr-B_Mask.gbs, uaeficopiedtovfr-B_Paste.gbp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]
2024-04-27 Mounting holes and resistor
    Added a mounting hole for the case, moved existing hole closer to corner, populated ADC3 resistor
2024-04-28 Holes and VR
    Rearranged bolt hole and VR conditioner to move hole closer to board edge
2024-04-28 Added ref to hole
2024-05-18 GHA says update kicad6-libraries
2024-05-27 Added spreadsheet with 0.04 rev A hardware fixes
    [0.04_hardware_mods.ods]
2024-05-27 Added VR- offset resistors and pads for unused analog/hall inputs
    [uaeficopiedtovfr.kicad_sch]
2024-05-27 fixed R17 silkscreen overlapping pad
2025-01-05 Changed to LM1815 for VR sensing, incremented revision to 0.05
    [IGN6.kicad_sch, INJ6.kicad_sch, LM1815-Cam.kicad_sch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]
2025-01-05 Added DNP parts to kicad bom
    [LM1815-Cam.kicad_sch, LM1815.kicad_sch]
2025-01-05 Trying to make BOM work
    [bom_replace_VFRECU-VR.csv]
2025-01-05 Fixed mismatch between part designators?
    [LM1815-Cam.kicad_sch]
2025-01-06 Missed two designators
    [LM1815-Cam.kicad_sch]
2025-01-06 Don't need proofreading I'm a FREAK
    [VFRECU-VR.kicad_sch]
2025-01-06 Removed vestigial pull up resistors on cam/crank - pins
2025-01-06 Edited designator instead of label
    [LM1815-Cam.kicad_sch, bom_replace_VFRECU-VR.csv]
2025-01-06 Fixed BOM filename
    [bom_replace_VFRECU-VR-0.05.csv]
2025-01-06 Cleared BOM
    [bom_replace_VFRECU-VR-0.05.csv]
2025-01-29 Lots of routing changes
    Read some papers by TI during a jenkem binge and hopefully improved the PCB layout
2025-02-03 More routing changes
    [LM1815-Cam.kicad_sch, VFRECU-VR.kicad_sch]
2025-02-03 Fixed references
    [bom_replace_VFRECU-VR-0.05.csv]
2025-02-05 Moved Ground Planes to Internal Layers
    [VFRECU-VR.kicad_sch]
2025-02-05 Routing and Silkscreen Improvements
2025-02-05 Changed ground vias on ignition drivers
2025-02-06 Fixed pads
    [VFRECU-VR.kicad_sch]
2025-02-06 made ground planes better
2025-02-10 Changed component sizes, added stitching vias
    [LM1815-Cam.kicad_sch, LM1815.kicad_sch]
2025-02-10 Changed ignition driver pad
2025-02-10 via fence around WBO heater
2025-02-13 Added knock detection hardware
    [VFRECU-VR.kicad_sch]
2025-02-18 Cleared ground plane under antenna
2025-02-18 Ground plane and via changes
2025-03-01 vias and silkscreen changes
